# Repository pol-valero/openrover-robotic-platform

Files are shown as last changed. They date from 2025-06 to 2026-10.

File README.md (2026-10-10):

# OpenRover robotic platform

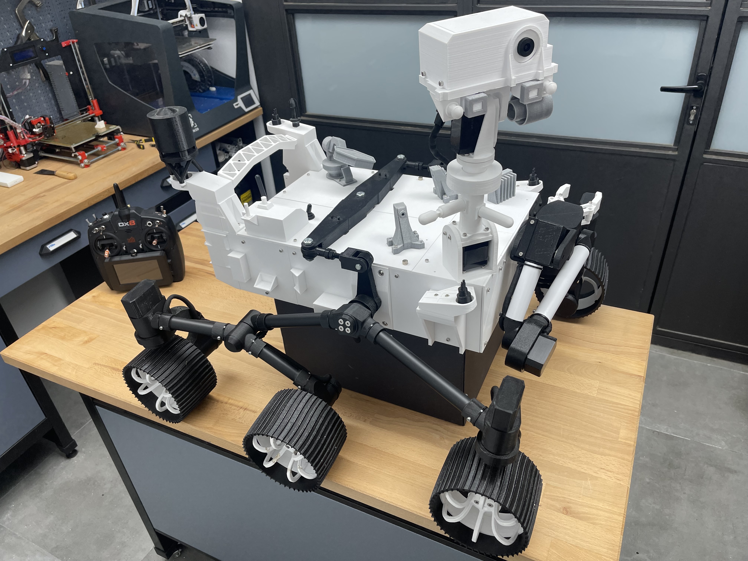
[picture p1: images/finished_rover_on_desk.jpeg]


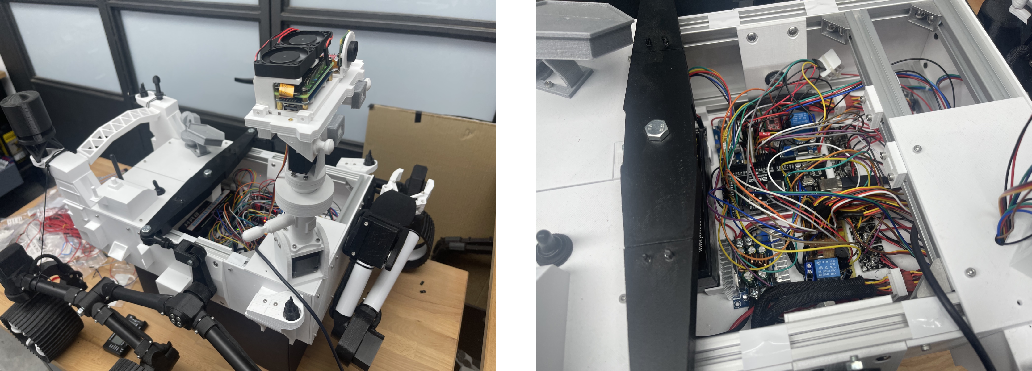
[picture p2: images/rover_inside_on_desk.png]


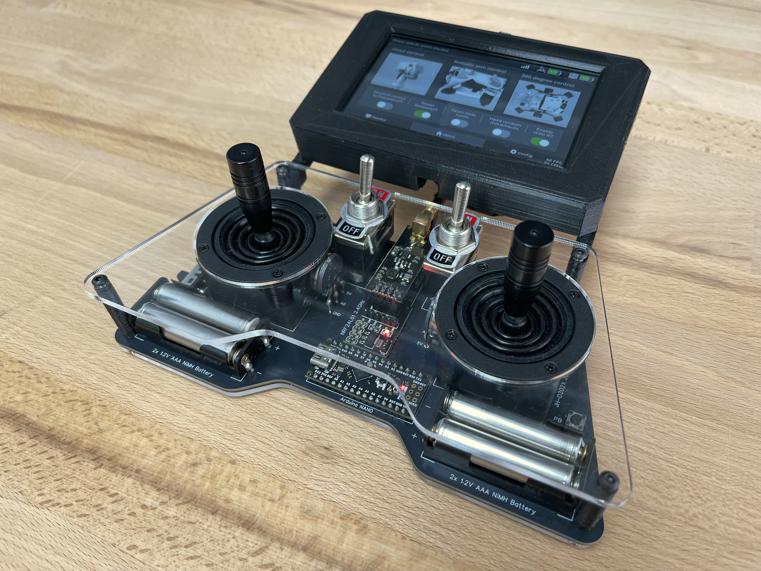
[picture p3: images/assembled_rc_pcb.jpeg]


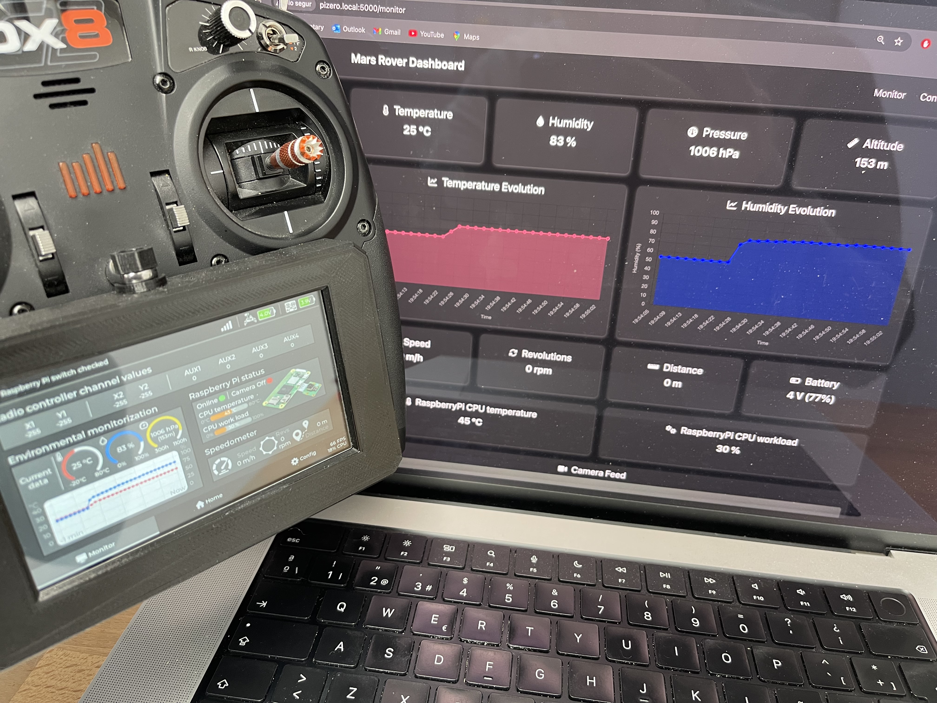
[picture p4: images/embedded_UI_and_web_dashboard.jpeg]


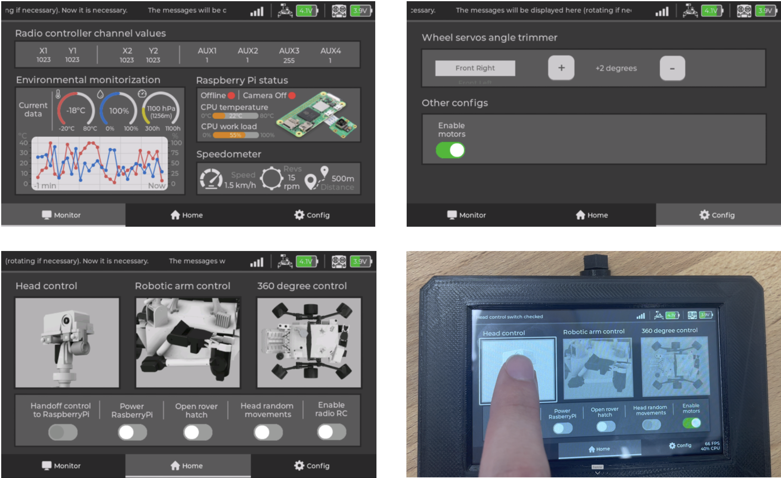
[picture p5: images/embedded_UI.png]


## Project overview

### Context
Rovers are planetary exploration robots that space agencies like NASA send to Mars or the Moon to explore and collect information, images, and samples. In this project, a functional 3D printed replica of the Mars "Perseverance" rover, which was launched by NASA in July 2020, is created. 

The OpenRover project was developed as part of my final computer engineering degree project. Therefore, in addition to the documentation provided in the repository’s READMEs, you can find a comprehensive [project report](project_report/openrover_project_report.pdf) containing theoretical explanations, design decisions, and technical implementation details (but the repository's READMEs provide enough information to replicate the project). 

### Objective
The main objective of the OpenRover project is to provide an extensible open-source robotic platform that allows anyone building it to put their DIY software/hardware/mechanical skills into practise, and to use popular development boards like Arduino, ESP32, and Raspberry Pi.  

As rovers are extremely sophisticated machines, they provide the perfect excuse to incorporate into the robotic platform several complex functionalities that replicate, at a smaller scale, the functionalities that real Mars rovers have (e.g., robotic arm, environmental sensors, 6-wheel drive, camera feed).  

### Key contributions
Although many similar open-source robotic projects already exist, even some also related to Mars rover robots, they tend to use a single type of development board. In the OpenRover project, several development boards are used among its main functional modules (e.g., RaspberryPi for web connectivity, ESP32 for embedded screen, Arduino for motor control) and there are interactions between these modules. 

This adds more educational value to the project, allowing to see some of the optimal usecases for each development board, and differentiates OpenRover from other open-source DIY robotic projects. 

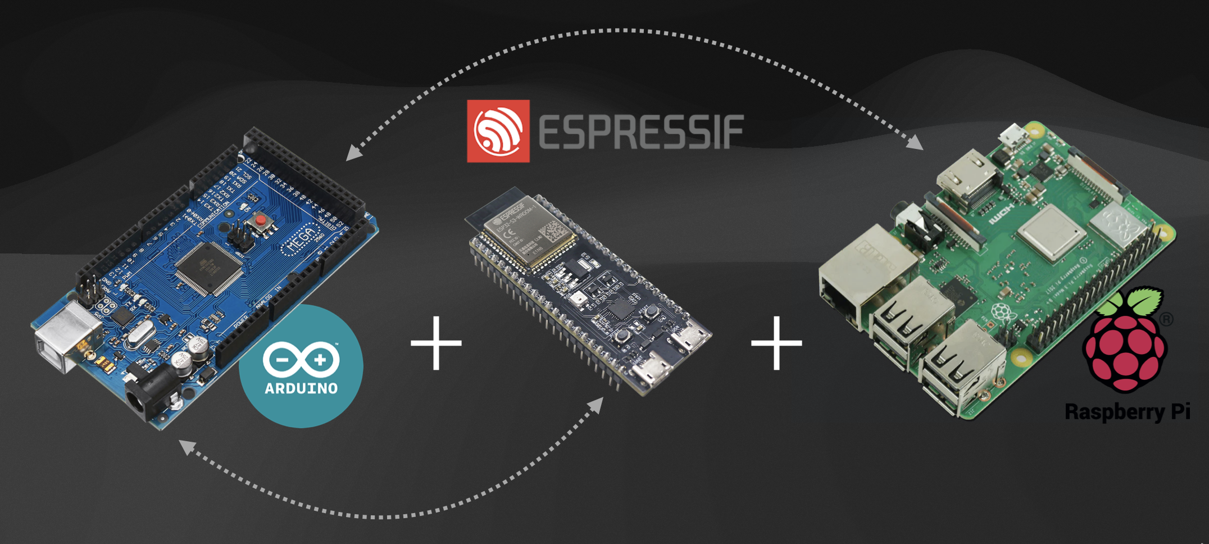
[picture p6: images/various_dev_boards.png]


### Tech stack

#### Programming languages and frameworks

 








#### Other technologies

To program Arduino and ESP32 microcontrollers, the PlatformIO IDE with the Arduino Framework was used. To create the embedded UI design of the touchscreen, the SquareLine Studio platform and LVGL library were used.

### Disclaimers
The rover's 3D design was originally made by a mechatronics engineer called Dejan, who owns an educational YouTube channel and website called "HowToMechatronics". This design was adapted and improved. 

**[Link to the original project used for the rover's 3D design](https://howtomechatronics.com/projects/diy-mars-perseverance-rover-replica-with-arduino/)**

The robotic arm's 3D design was extracted from a GitHub project made by Jakob Krantz, who also created a Mars rover replica. This design was adapted and improved. 

**[Link to the original project used for the robotic arm's 3D design](https://github.com/jakkra/Mars-Rover)**

All the OpenRover hardware and software was created from scratch, following a different approach from the one the creators of the original 3D designs followed. 

## Features

The OpenRover platform offers an interesting set of functionalities:

- 6-wheel drive platform with 4 steerable wheels
- 4-axis foldable robotic arm with gripper
- Tiltable and rotary head, with space for a development board and a camera
- Environmental sensors to measure temperature, humidity, pressure and altitude
- Custom remote control module with touchscreen, with a UI where status values are displayed and different operation modes can be selected
- Battery sensors for the rover and the custom remote control
- 4 main operation modes: conventional driving control, 360º turn control, robotic arm control, head control
- Web dashboard that displays status values and a video feed. This web dashboard is hosted in the rover

## Project modules
The OpenRover's components are organized, both at a hardware and software level, in different modules:

- [Central rover module](central_rover_module/): It has an Arduino Mega development board located inside the main body of the rover which manages all moving elements (e.g., motors, servomotors) as well as the rover's sensors and sending/receiving the radio signal.

- [Remote control and touchscreen module](remote_control_and_touchscreen_module/): It has an ESP32S3 development board that is responsible for managing the touchscreen, and an Arduino Nano that is responsible for reading the RC channel values, sending/receiving the radio signal and measuring battery levels. Two different remote control versions are available: a custom remote control PCB, or an attachment for a generic/commercial remote control.

- [Camera and webserver module](camera_and_webserver_module/): It has a RaspberryPi Zero 2W development board located inside the head of the rover. This board connects to a camera, generates a WiFi network and hosts a web dashboard.

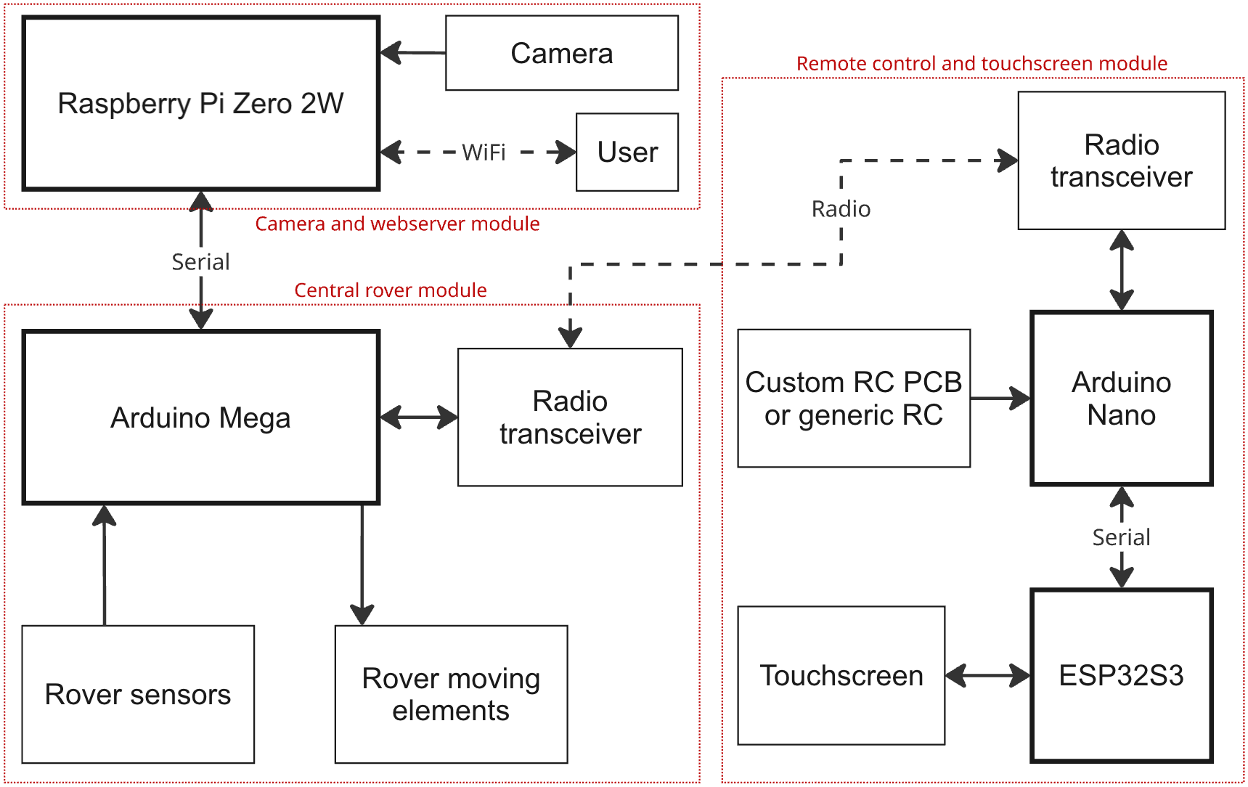
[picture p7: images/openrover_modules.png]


### Remarks
This repository contains the code and documentation of all the modules. However, the codebase is actually distributed across different repositories:

- The folder ``camera_and_webserver_module/raspberrypi_code/`` contains the [openrover-web-dashboard](https://github.com/pol-valero/openrover-web-dashboard.git) repository. 

- The folder ``central_rover_module/arduino_mega_code/`` contains the [openrover-central-controller](https://github.com/pol-valero/openrover-central-controller) repository. 

- The folder ``remote_control_and_touchscreen_module/pcb_remote_control/arduino_nano_code/`` contains the [openrover-rc-transmitter-pcb](https://github.com/pol-valero/openrover-rc-transmitter-pcb) repository. 

- The folder ``remote_control_and_touchscreen_module/generic_remote_control_attachment/arduino_nano_code/`` contains the [openrover-rc-transmitter](https://github.com/pol-valero/openrover-rc-transmitter) repository. 

- The folder ``remote_control_and_touchscreen_module/esp32s3_code/`` contains the [openrover-rc-touchscreen](https://github.com/pol-valero/openrover-rc-touchscreen.git) repository. 

- The folder ``remote_control_and_touchscreen_module/touchscreen_ui_design_squareline/`` contains the [openrover-touchscreen-ui-design](https://github.com/pol-valero/openrover-touchscreen-ui-design.git) repository. 

"Git subtrees" were used to link these independent repositories to folders inside this central [openrover-robotic-platform](https://github.com/pol-valero/openrover-robotic-platform) repository. 

## Expected build time
The build time can vary a lot depending on skill level and number of tools available. Experienced builders can expect to assemble the mechanical platform in approximately 60 hours and implement all the wiring and hardware in approximately 80 hours. 

Although the exact number of 3D printing hours was not recorded, it is estimated that it took approximately 400 hours to 3D print all the rover’s components. This number can vary a lot depending on the 3D printer model and the desired 3D printing quality.

## Getting started steps
- Step 1: Order all the mechanical and hardware parts. Lists with the most important parts are provided in the [hardware components](hardware_components/) folder.

- Step 2: 3D print the rover and remote controller parts present in the 3D design files, which are detailed inside the [3D designs](3d_designs/) folder.

- Step 3: Assemble the mechanical platform by joining the different 3D printed parts with the other mechanical parts (e.g., aluminium profiles, PVC tubes). A detailed guide for the mechanical assembly process of the rover is available in the [original project used for the mechanical design](https://howtomechatronics.com/projects/diy-mars-perseverance-rover-replica-with-arduino/). Images showing the assembly of the modified OpenRover design and custom remote control are available in the [assembly folder](assembly/).

- Step 4: Create the wiring connections for the hardware components (e.g., motors, servomotors) and between the hardware electronics (e.g., Arduino Mega, motor drivers). In each of the OpenRover's modules folders ([central rover](central_rover_module/), [remote control and touchscreen](remote_control_and_touchscreen_module/), and [camera and webserver](camera_and_webserver_module/)), schematics of the wiring connections are found. Images showing the soldering of various boards, the creation of electrical connections, and the placement of hardware components can be found in the README of the [assembly folder](assembly/).

- Step 5: Set up and upload the code to the development boards. In each of the OpenRover's modules folders ([central rover](central_rover_module/), [remote control and touchscreen](remote_control_and_touchscreen_module/), and [camera and webserver](camera_and_webserver_module/)), additional README files detail the necessary steps for getting all the OpenRover's software up and running for the module.

## Demos
| |  |
| --- | --- |
|  |  |
|  |  |

### Longer demo video
Here is a longer demo video where some of the possible movements can be seen: https://www.youtube.com/watch?v=uD4_qy3aUkQ

Preview of demo video at 2x speed: 



### More images
On the [sciencefairs and makerfaires images](images/sciencefairs_and_makerfaires_images/) folder, there are some more images of the rover in action as well as an image detailing how the rover can be disassembled for easier transport. 

## Take it to the next level
Now it is your time to build upon the OpenRover platform. One of the cores ideas behind OpenRover is that people who replicate the project are able to modify and improve the platform, as it is designed to be very modular and extensible, specially on the software related side. 

You can add your own upgrades to the robot, integrating new components and developing additional features. 

Here are some ideas to spark inspiration for expanding OpenRover's functionalities:

- Rover control from the web dashboard (e.g., using draggable joysticks), which currently is only used for monitoring and displaying video feed

- Adding computer vision using the existing RaspberryPi camera and RaspberryPi Zero 2W board. Computer vision could be used to navigate autonomously or to track objects with the rover's tiltable and rotary head

- Ability to record movements for the robotic arm, allowing it to automatically fold and unfold or perform a certain procedure

- From the hardware schematic designs of the rover, design PCB boards that can be manufactured. These boards would be very useful to make the hardware connections more compact and to allow an easier replication of the project

<br/>

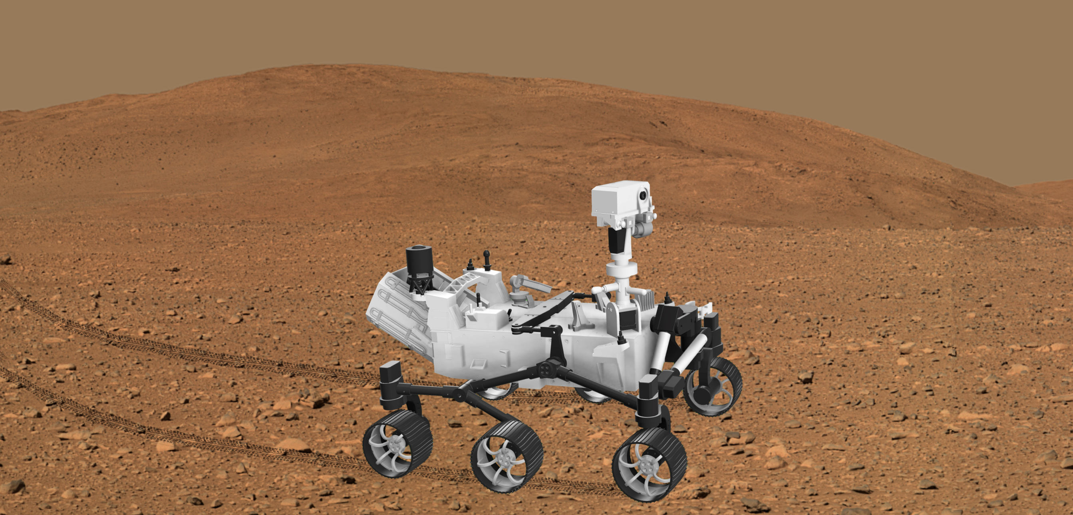
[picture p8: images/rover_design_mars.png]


## Licensing
Licensed under [MIT License](LICENSE.txt)

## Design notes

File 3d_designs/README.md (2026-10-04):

## 3D designs remarks

The original 3D design of the Mars rover model can be found in this [Cults3D page](https://cults3d.com/en/3d-model/game/mars-rover-perseverance-replica-howtomechatronics). The original 3D design of the robotic arm can be found in this [GitHub page](https://github.com/jakkra/Mars-Rover). Lots of modifications were made to these designs, which were originally created by Dejan (HowToMechatronics) and Jakob Krantz respectively.

Since the original design of the Mars rover is not free (it has to be purchased via the Cults3D page provided before) only the parts of the rover that were created from scratch are present in the [rover Fusion360 design file](rover_modified_and_new_parts.f3d) of this folder. Since the original design of the robotic arm is open-source, the [rover Fusion360 design file](rover_modified_and_new_parts.f3d) contains the parts of the robotic arm that were either created from scratch, modified or original. 

For the remote control and touchscreen module, there are two different 3D designs depending on the selected option:

1) Custom remote control PCB: This [Fusion360 design file](rc-pcb-spacers-and-touchscreen-case.f3d) contains the spacers that hold the acrylic plates and PCB together, the structure that holds the touchscreen, and the case for the ESP32S3-8048 touchscreen.

2) Generic/commercial remote control attachment: The cases for the home-made PCB (of the "Arduino Nano" submodule) and for the ESP32S3-8048 touchscreen are in this [Fusion360 design file](rc_and_touchscreen_cases-spektrum_dx8.f3d). These cases adapt to the shape of the Spektrum DX8 remote, allowing to place the home-made PCB and touchscreen as an attachment. 

The case for the ESP32S3-8048 touchscreen is a modified version of this [case design](https://www.thingiverse.com/thing:6517481) found on Thingiverse.

## 3D designs images

### DIY Perseverance Rover Replica design with some new and modified parts
  <p align="center">
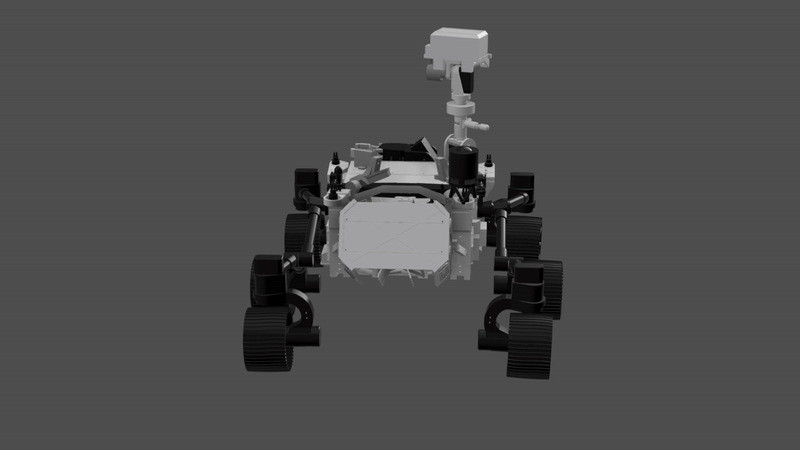
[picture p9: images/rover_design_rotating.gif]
animated
    
  </p>

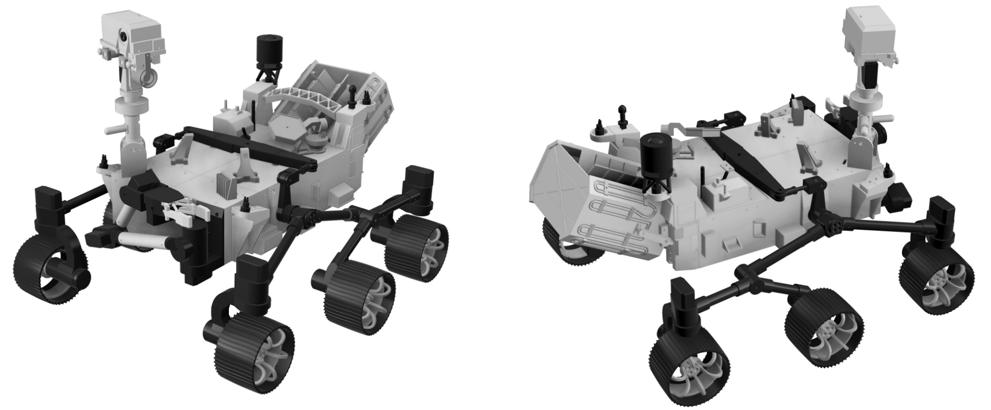
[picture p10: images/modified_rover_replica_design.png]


### Original (left) and modified (right) robotic arm design
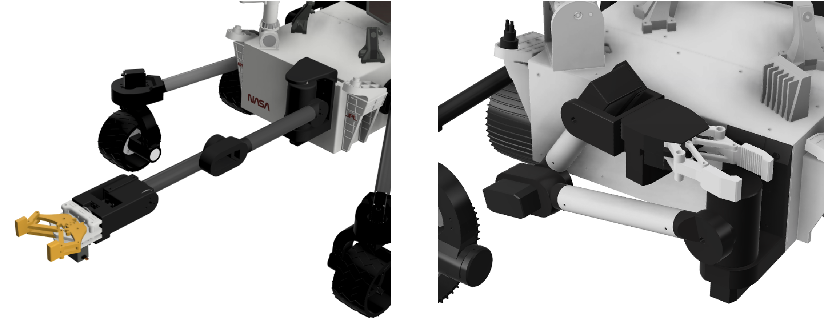
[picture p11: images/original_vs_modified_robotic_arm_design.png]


### Spacers, touchscreen case, and structure design for the custom remote control PCB 
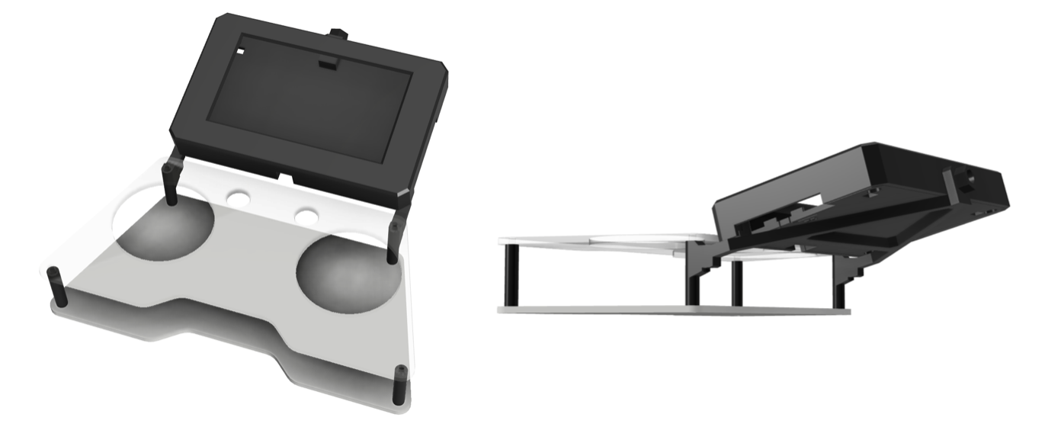
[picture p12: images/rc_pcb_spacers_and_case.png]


### Attachment cases design for the generic/commercial remote control 
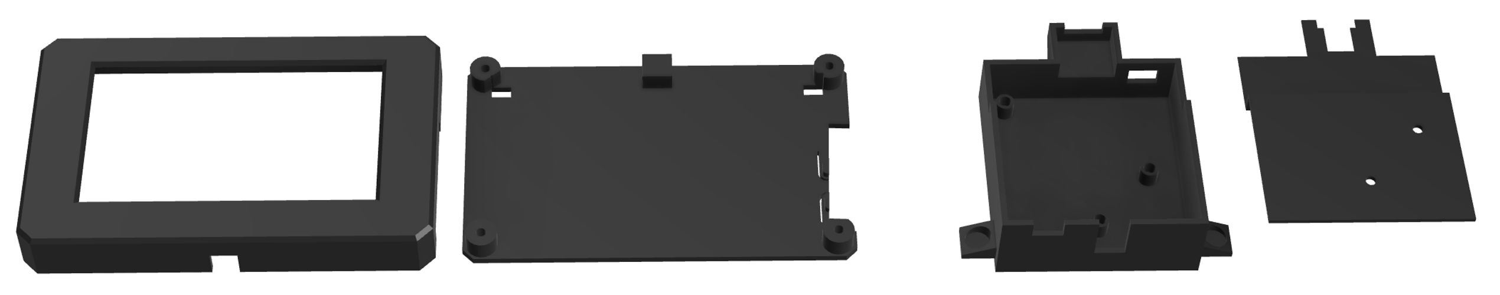
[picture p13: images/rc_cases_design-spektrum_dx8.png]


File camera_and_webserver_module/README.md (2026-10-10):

# Camera and webserver module
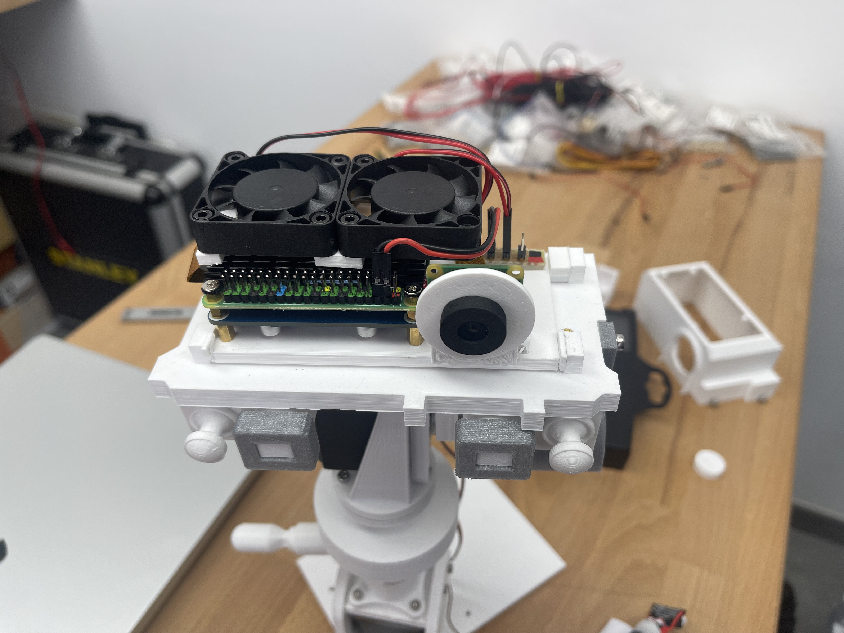
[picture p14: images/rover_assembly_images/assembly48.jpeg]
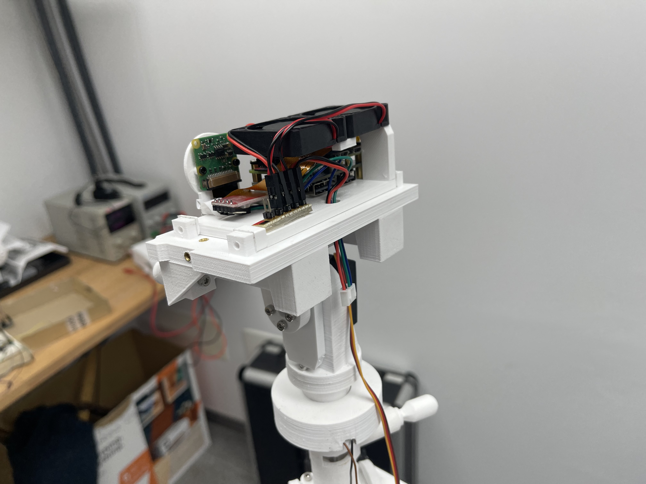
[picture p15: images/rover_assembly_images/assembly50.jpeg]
|  |  |
| --- | --- |

## Code setup guide
Before uploading this module's project code in the RaspberryPi Zero 2W, it is necessary to install and OS in the board. Specifically, the RaspberryPi OS Lite (headless version) has to be installed. This OS and an install guide can be found in the [RaspberryPi website](https://www.raspberrypi.com/software/operating-systems/).

Once the Raspberry Pi OS is running and SSH connections can be made to be the board, it is possible to upload all the module's project code. To upload an edit the code, the best way is to install the SFTP plugin for the Visual Studio Code editor. This plugin allows to easily set up and modify the project’s file structure and file’s contents remotely from a standard PC. 

Once the whole project is uploaded, you have to go inside the main project folder and execute the following command. 

```python -m logic.main```

If it is the first time you execute this command, several errors will displayed, detailing the dependencies used by the code that need to be installed. It is recommended to install this dependencies on a "virtual environment". Once these dependencies are installed, if we execute the previous command, this module's program will start running, stablishing serial communication with the Arduino Mega and generating the web dashboard. 

The web dashboard will be available on the following URL. 
```http://pizero.local:5000/monitor```

If instead of the RaspberryPi connecting to an existing WiFi, you want the RaspberryPi to generate a WiFi network on its own, the following command needs to be used.   
```sudo nmcli device wifi hotspot ssid RoverWiFi password marsRover```

Optionally, the commands to generate the WiFi network and to execute the module's program can be written into a script. This script can then be called inside the ```/etc/rc.local``` file, which is executed at startup. This way, once the RaspberryPi Zero 2W is powered, it will generate the WiFi network and execute the module's program automatically. You can find and example startup script in the [raspberrypi_code/scripts/](raspberrypi_code/scripts/) folder.

It is important to make sure that the wiring connections to the RaspberryPi Zero 2W are exactly the same as the ones detailed in the wiring schematic of this module.

## Web dashboard UI design
The implemented monitoring screen can be seen in the image below. 

![Alt text](/images/web_dashboard_computer.png)

The web dashboard design is responsive and adapts to different screen sizes, as seen in the images below. 

![Alt text](/images/web_dashboard_mobile.png)

## Hardware and schematics
The hardware present on the camera and webserver module includes a RaspberryPi Zero 2W board that is responsible for receiving camera input, creating a WiFi network with a self-hosted website available in it and sending/receiving communications via serial (to/from Arduino Mega).

In this [schematic](camera_and_webserver_module_schematic.pdf), all the hardware present on this module can be seen.

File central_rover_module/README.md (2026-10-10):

# Central rover module
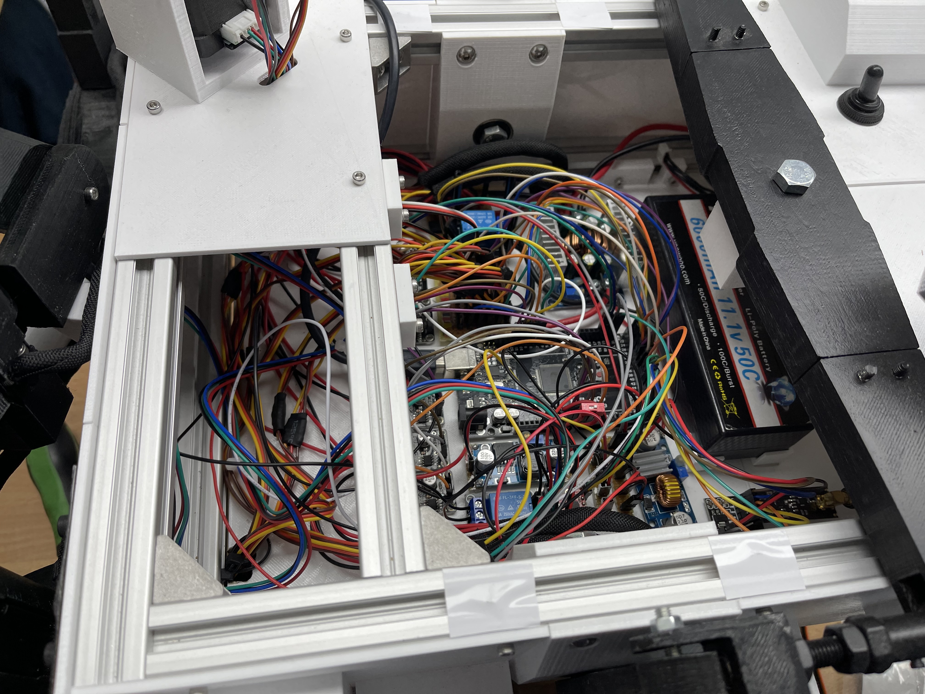
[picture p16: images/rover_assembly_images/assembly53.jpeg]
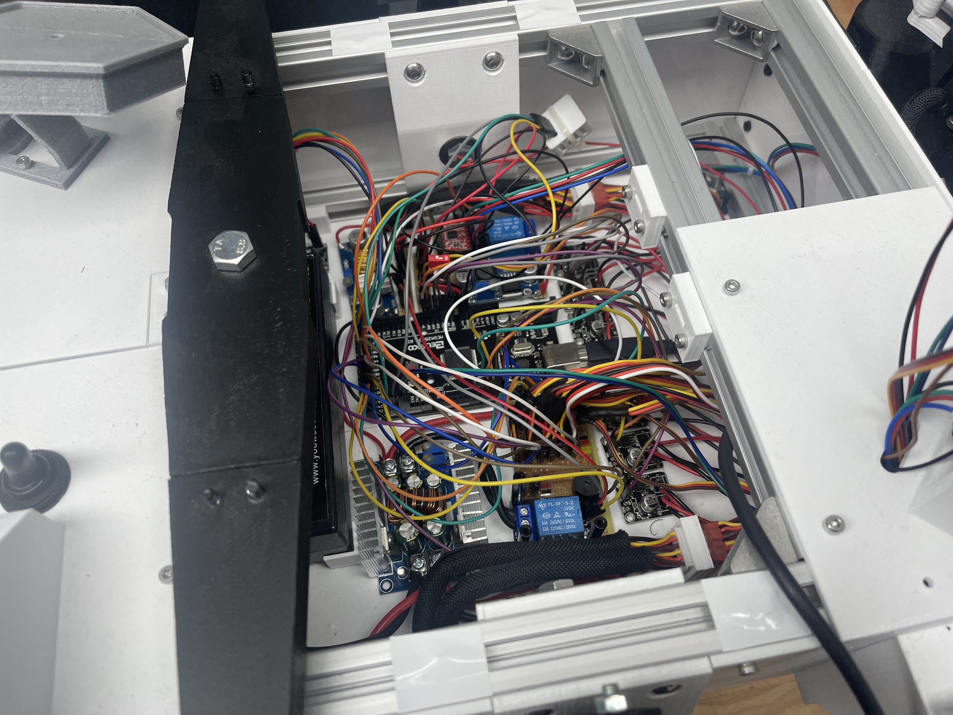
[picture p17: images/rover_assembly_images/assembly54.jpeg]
|  |  |
| --- | --- |

## Code setup guide
To develop the code for this module, the PlatformIO IDE was used. This IDE is integrated into the versatile Visual Studio Code editor, and can be installed simply by searching "PlatformIO IDE" in the "Extensions" tab of Visual Studio Code. 

Thanks to the use of PlatformIO, all the code, configuration files, and dependencies are in a single package. This makes it very easy to share the complete project, enabling other people to execute it right after they download it. 

Therefore, just by opening the project present in this folder with PlatformIO, connecting the Arduino Mega development board via USB, and clicking the "upload" button, the code will be uploaded to the Arduino Mega and will start executing. 

The only thing that needs to be taking into account is making sure that the wiring connections to the Arduino Mega are exactly the same as the ones detailed in the  wiring schematic of this module. 

## Hardware and schematics
The hardware present on the central rover module includes an Arduino Mega development board that is responsible for managing all the moving elements (e.g., servomotors, motors, stepper motor), reading the environmental sensor’s values and sending/receiving communications via serial (to/from RaspberryPi Zero board) and via radio (to/from custom RC). 

In this [schematic](central_rover_module_schematic.pdf), all the hardware present on this module can be seen.

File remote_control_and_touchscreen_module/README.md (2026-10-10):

# Remote control and touchscreen module

## Remote control options
The OpenRover project has two remote control options available:

1) Custom remote control created from scratch, using a manufactured double-layer PCB, some 3D printed parts, and acrylic plastic. Code, schematics, and further info can be found in this [folder](pcb_remote_control/). 

2) Custom attachment for a generic/commercial remote control that has a PPM output port, like the Spektrum DX8, using a home-made PCB and some 3D printed parts. Code, schematics, and further info can be found in this [folder](generic_remote_control_attachment/).

For anyone trying to replicate the project, I would definitely recommend choosing the first option. The second option would only be suited for those who already have a Spektrum DX8 (or similar) remote control, really like how it feels/handles, and would like to tinker with it. For the second option, also note that from my experience, the PPM readings can be a little unreliable sometimes.

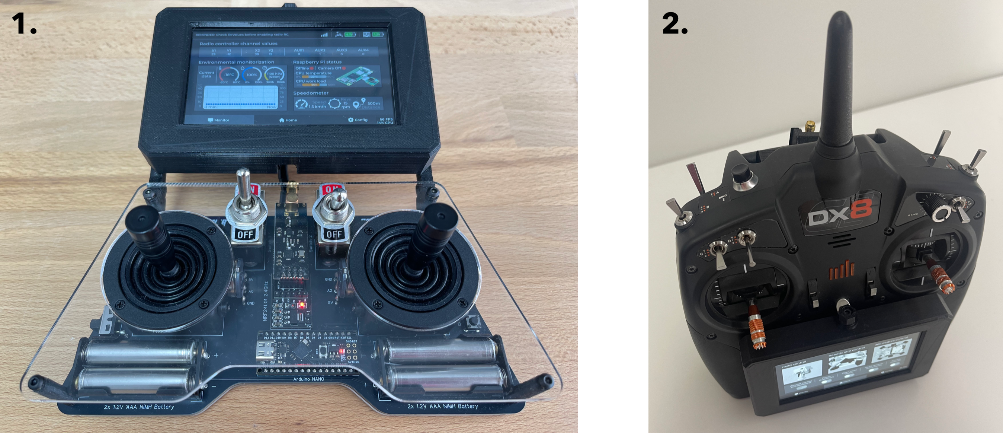
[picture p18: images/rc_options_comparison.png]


## Code setup guide
No matter which remote control option is selected, this module is formed by two submodules, the "Arduino Nano" and the "ESP32S3 touchscreen" submodules. The [code](esp32s3_code/) and [embedded UI design](touchscreen_ui_design_squareline/) of the "ESP32S3 touchscreen" submodule is exactly the same for the two remote control options, that's why they are located in this folder. The code and schematics of the "Arduino Nano" submodule and the schematics of the "ESP32S3 touchscreen" submodule differ depending on the chosen remote control option, that's why they are located inside the folder of each remote control option.

To develop the code for these submodules, the PlatformIO IDE was used. This IDE is integrated into the versatile Visual Studio Code editor, and can be installed simply by searching "PlatformIO IDE" in the "Extensions" tab of Visual Studio Code. 

Thanks to the use of PlatformIO, all the code, configuration files, and dependencies are in a single package. This makes it very easy to share the complete project, enabling other people to execute it right after they download it. 

Each of the two submodules is a standalone PlatformIO project. Therefore, just by opening the project present in this folder (and in the chosen RC option subfolder) with PlatformIO, connecting the ESP32S3 or Arduino Nano development board via USB, and clicking the "upload" button, the code will be uploaded to the ESP32S3 or Arduino Nano and will start executing. 

The only thing that needs to be taking into account is making sure that the wiring connections of the ESP32S3 and the Arduino Nano are exactly the same as the ones detailed in the wiring schematics of this module, which can be found inside the folder of each remote control option. 

## Embedded UI design
To create the embedded UI design of the touchscreen, the SquareLine Studio platform and LVGL library were used. To edit the UI, these steps have to be followed:

- Step 1: Open the [SquareLine Studio project](touchscreen_ui_design_squareline/) and make the desired visual changes

- Step 2: Click on Export -> Export UI Files. The UI files export path must be previously specified in the "Project Settings"

- Step 3: Copy all the exported UI Files into the "squareLineFiles" folder of the [ESP32S3 PlatformIO project](esp32s3_code/), making sure to overwrite the previous files that were in this folder

- Step 4: Click the "upload" button in PlatformIO to upload the code to the ESP32S3. The modified UI should now appear on the touchscreen. 

Three screens have been implemented in the embedded UI: Control, Monitor and Configuration. These screens can be seen in the images below. 

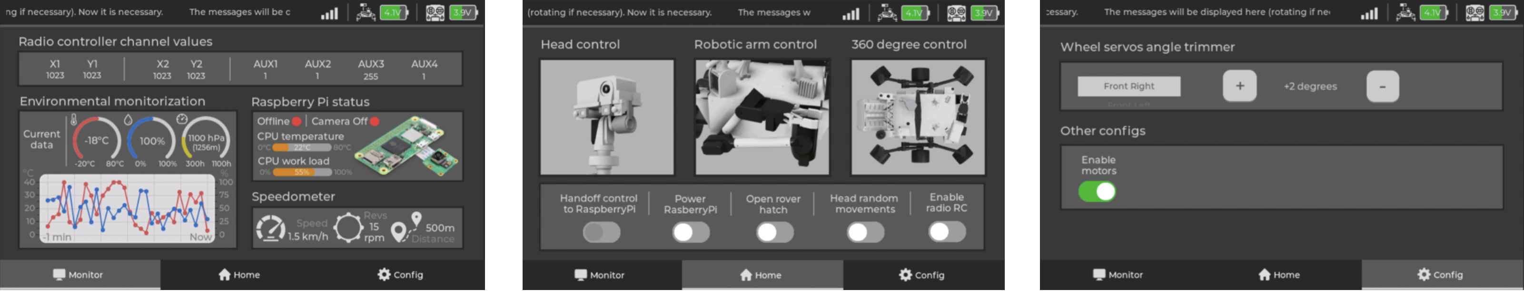
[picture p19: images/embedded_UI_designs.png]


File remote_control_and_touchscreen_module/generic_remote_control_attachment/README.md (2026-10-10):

# Attachment for a generic/commercial remote control
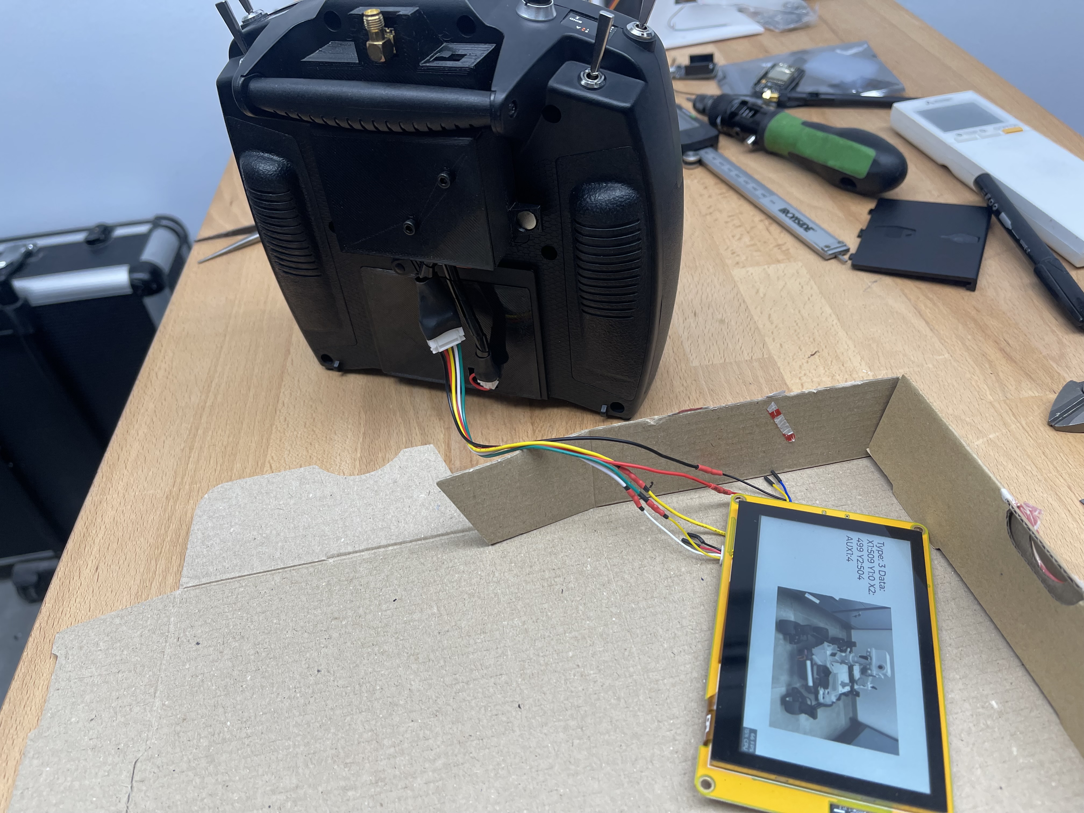
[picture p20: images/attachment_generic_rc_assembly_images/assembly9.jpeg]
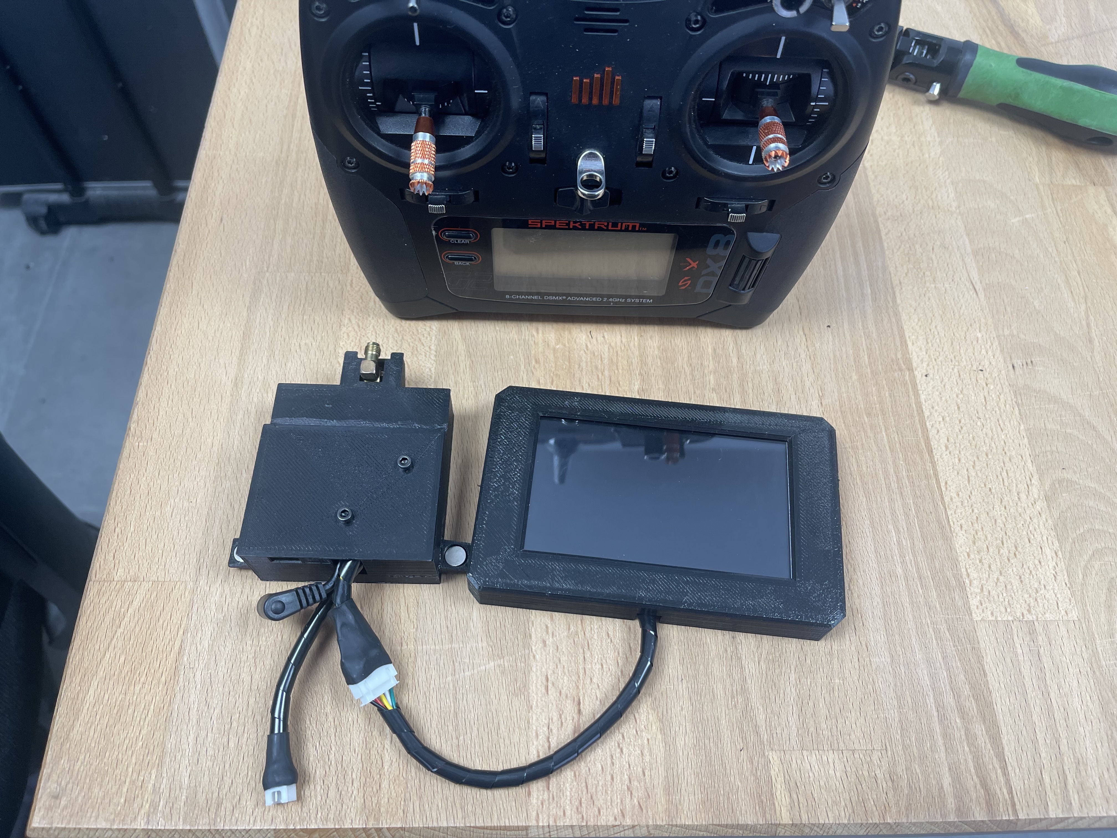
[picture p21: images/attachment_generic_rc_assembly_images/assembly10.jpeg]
|  |  |
| --- | --- |

## Remarks
For this remote control option, the developed remote control and touchscreen module is an attachment for any generic/commercial RC that has a PPM output port (usually known as "Trainer Port"). The RC model that I have personally used is the Spektrum DX8 (if another model wants to be used, the 3D printed parts would have to be adapted). 

This trainer port usually is a 3.5mm audio jack, but it is not a standard port and could also be a mini-USB, depending on the brand. The transmitters usually use PPM (Pulse Position Modulation) signals outputted from this “Trainer port” to transmit each of the RC channel values.

With the help of an Arduino Nano, these PPM signals can be processed by the custom attachment that was developed. This way, the radio module of the generic RC is not used, and the only purpose of the generic RC is to send the values of its different channels (e.g., joysticks, switches…) via PPM, so that the custom attachment can receive them. In turn, this custom attachment uses an NRF24 radio transceiver to send the channel values to the rover using a custom communication protocol. 

## Hardware and schematics
For this option (generic remote control attachment), the hardware present in this module includes an ESP32S3 development board that is responsible for managing the screen and an Arduino Nano board that processes the RC PPM signals, reads the battery voltage, and controls the radio transceiver. 

The touchscreen model is the ESP32S3_8048S043, with a resolution of 800 x 480 px and 4.3" screen size. This model has an ESP32S3 and I/O connectors built in.

This is the [schematic](rc_and_touchscreen_module_schematic-generic_remote.pdf) for this remote control option, where all the hardware present on this module can be seen.

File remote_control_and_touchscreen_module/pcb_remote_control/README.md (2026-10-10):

# Custom remote control PCB
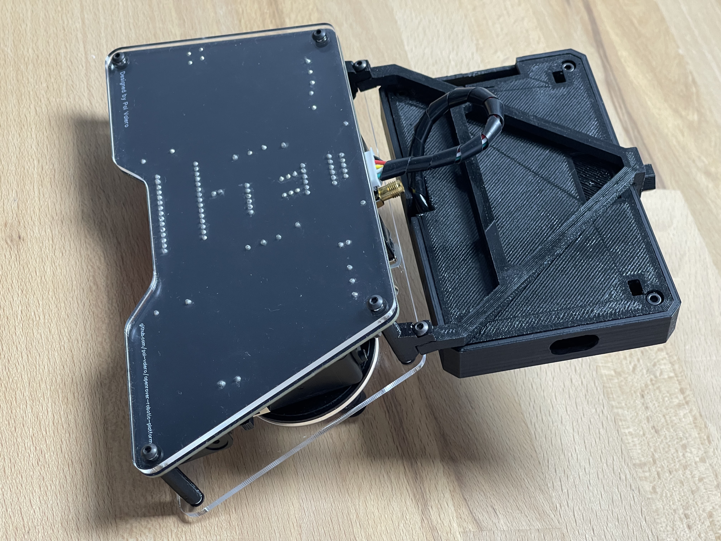
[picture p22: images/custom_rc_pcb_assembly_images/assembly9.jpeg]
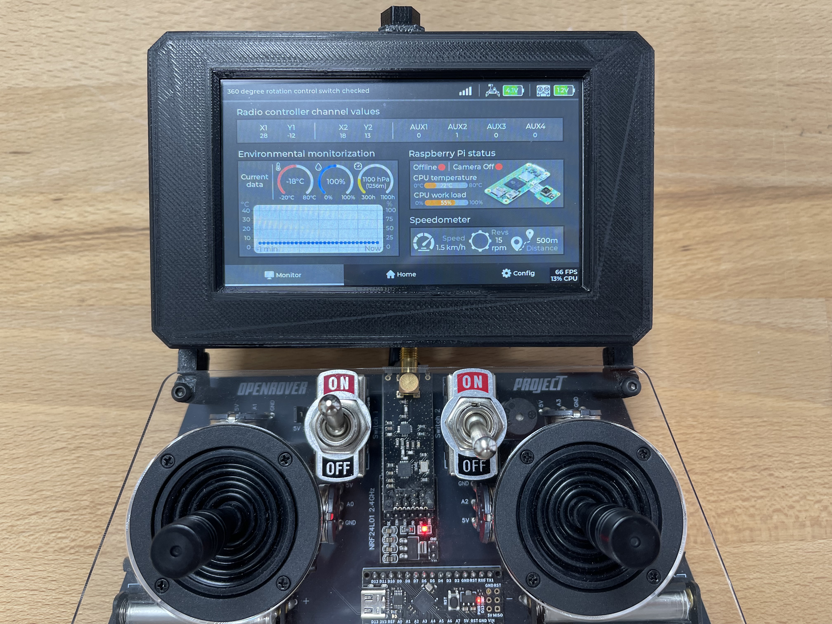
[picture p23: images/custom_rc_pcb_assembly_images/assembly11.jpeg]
|  |  |
| --- | --- |

## Remarks
For this remote control option, the developed remote control and touchscreen module is built using a custom double-layer PCB. The [PCB design](remote_control_pcb_design_easyeda.json) has been created using the EasyEDA app, and the PCB has been manufactured by JLCPCB. 

In order to manufacture the PCB, a [Gerber fabrication file](remote_control_pcb_gerber.zip) has to be generated from the design and then has to be uploaded to the manufacturer's website (e.g., JLCPCB, PCBWAY...). If you want to make any modifications to the EasyEDA PCB design, you will have to regenerate the Gerber by going into the top menu and selecting "Fabrication -> PCB Fabrication File (Gerber) -> Generate Gerber".

Other parts of the remote control that have to be manufactured are the top and bottom acrylic plates, which should be cut using a laser or CNC machine. In my case, I used a workshop near my home that had a laser machine, but there are also online websites where you can order laser cut designs in acrylic. These are the designs for the [top](rc_top_plate.dxf) and [bottom](rc_bottom_plate.dxf) acrylic plates. I would recommend using 3mm clear acrylic.     

## Hardware and schematics
For this option (custom remote control PCB), the hardware present in this module includes an ESP32S3 development board that is responsible for managing the screen and an Arduino Nano board that reads the analog or digital signals from the joysticks/switches/buttons, reads the battery voltage, and controls the radio transceiver. 

The touchscreen model is the ESP32S3_8048S043, with a resolution of 800 x 480 px and 4.3" screen size. This model has an ESP32S3 and I/O connectors built in.

This is the [schematic](esp32s3_touchscreen_submodule_schematic-pcb_remote.pdf) of the "ESP32S3 touchscreen" submodule for this remote control option. The [EasyEDA PCB design](remote_control_pcb_design_easyeda.json) can be seen as the schematic of the "Arduino Nano" submodule. 

Here are a couple images of the top and bottom layers of the EasyEDA PCB design:
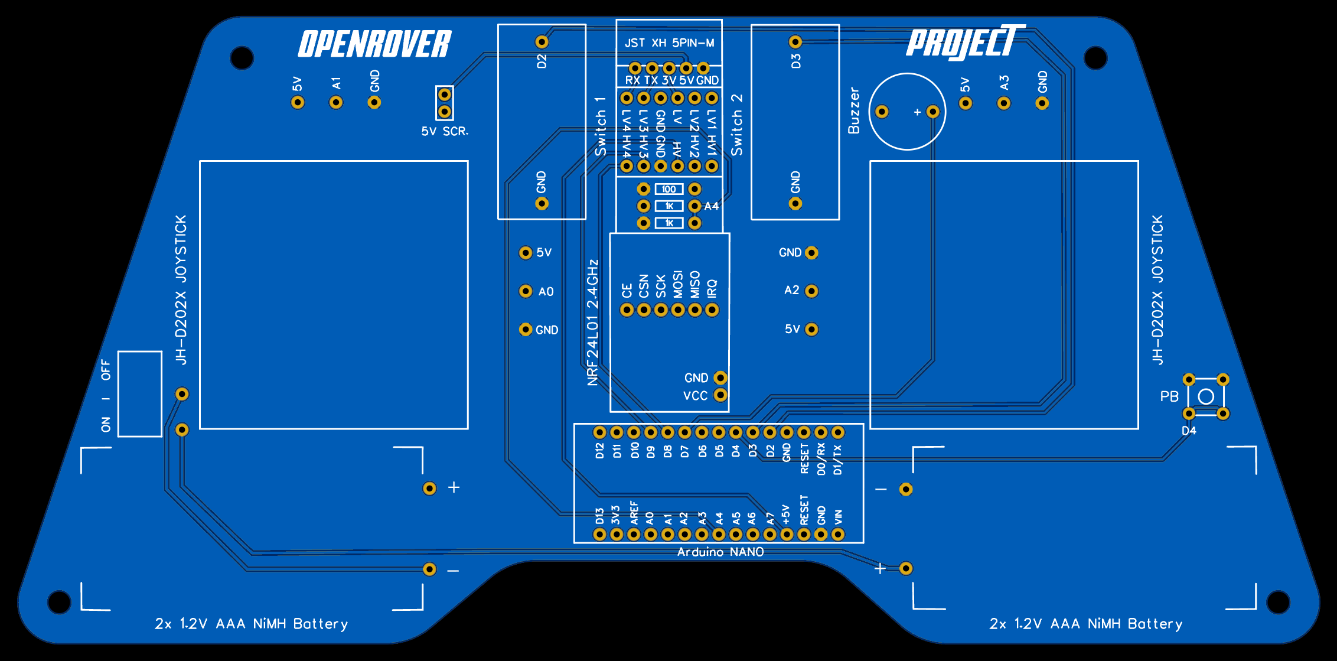
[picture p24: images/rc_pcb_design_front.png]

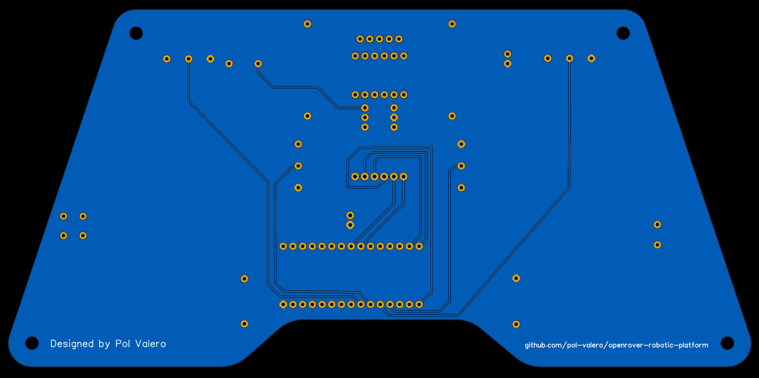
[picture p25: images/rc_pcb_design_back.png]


## Short demo


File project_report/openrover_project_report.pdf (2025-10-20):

# OpenRover: A 3D-printed open-source robotic platform for software and hardware development

# Pol Valero Arjona

# La Salle Campus Barcelona – Grau en Enginyeria Informàtica

# Barcelona, Juny 2025

i

# Abstract

Rovers are planetary surface exploration robots that space agencies like NASA send to Mars in order to explore and collect information that will be sent back to Earth.

This final degree project originates from a personal hobby project in which, using an existing 3D design of a Mars rover replica found online, the design has been adapted, improved, 3D printed and assembled at home. The final 3D printed result has the functional structure and appearance of the "Perseverance" rover, which was launched by NASA in July 2020, and landed on Mars in February 2021.

The main objective of the final degree project is to develop an open-source robotic platform that can enable anyone who tries building it to learn more about both the software and hardware aspects of DIY robotic projects, specially using and learning about widely adopted microcontrollers such as "Arduino" and "ESP32". As rovers are extremely sophisticated machines, they provide the perfect excuse to incorporate into the robotic platform several complex functionalities that replicate, at a smaller scale, the functionalities that real Mars rovers have (e.g., robotic arm, environmental sensors, 6-wheel drive).

Although many open-source robotic projects already exist (even some also related to Mars rover robots), they usually only use a single type of development board. In the developed OpenRover project, partly due to its complexity and wide scope, several development boards are used among its main functional modules (e.g., RaspberryPi for web connectivity, ESP32 for embedded screen, Arduino for motor control) and there are interactions between these modules. This adds more educational value to the project, allowing to see each development board optimal usecase, and differentiates OpenRover from other open-source DIY robotic projects.

Starting from the 3D printed structure of the rover, this project has incorporated into the rover all the hardware (e.g., motors, microcontrollers, sensors) as well as developed all the software (e.g., web dashboard for monitorization, creation of communication protocols between modules, generation of control signals for motors) that is necessary in order to operate the rover remotely. Additionally, a remote control module with a touchscreen has also been developed, which serves both as a means to operate the rover and to monitor its status in a graphical way.

The project has been named OpenRover, due to the "open source" nature of the project. OpenRover has been able to meet its main objective, as the created robotic platform and remote control module have incorporated several interesting functionalities using different development boards (Arduino, ESP32, RaspberryPi), making this project a useful resource for people wanting to learn more about the DIY robotics field, or for those who want to replicate and build upon the OpenRover robotic platform.

Keywords – Robotics, RaspberryPi, Arduino, ESP32, LVGL, Web dashboard, Embedded system

viii

ix

# Contents

x

xi

6.1 | Temporal costs | 88
6.2 | Economic costs | 89
7 | Conclusions | 90
8 | Future lines of work | 92
9 | References | 94
Annex I | 99
Annex II | 104

xii

# List of figures

Figure 6. Rover modified design and assembled mechanical structure (own elaboration of images

Figure 18. Key header and implementation files for central rover module (own elaboration) . 55

Figure 21. Central rover module “Execute frame type functions” activity (own elaboration)... 58

Figure 25. SquareLine studio components with default theme and configuration (own

Figure 27. Key header and implementation files for ESP32S3 and touchscreen submodule (own

Figure 28. Library headers and main.cpp file for Arduino Nano submodule (own elaboration) 66 Figure 29. ESP32S3 and touchscreen submodule main activity diagram (own elaboration) ..... 66 Figure 30. ESP32S3 and touchscreen submodule “Execute frame type functions” activity (own

Figure 31. ESP32S3 and touchscreen submodule buttons and switches flow (own elaboration)

Figure 34. Key implementation files and libraries for camera and webserver module (own

Figure 36. Camera and webserver module “Handle received frames thread” activity (own

xiii

Figure 37. Camera and webserver module “Manage status data thread” activity (own
elaboration) | 72
Figure 38. Camera and webserver module “Flask webserver threads” activity (own elaboration)
| 73
Figure 39. Web dashboard monitor screen (own elaboration) | 76
Figure 40. Web dashboard in mobile browser (own elaboration) | 77
Figure 41. Web dashboard and embedded UI comparison (own elaboration) | 77
Figure 42. RaspberryPi startup bash script (own elaboration) | 78
Figure 43. Tasks timing using non-blocking “millis()” template (own elaboration) | 81
Figure 44. C++ (left) and Python (right) frame structure (own elaboration) | 81
Figure 45. Frame types definition C++ header file (own elaboration) | 82
Figure 46. Project’s time distribution pie chart (own elaboration) | 88
Figure 47. Project’s Gantt diagram (own elaboration) | 89
Figure 48. Original DIY Perseverance Rover Replica design (own elaboration of images and
original design extracted from [9] ) | 99
Figure 49. Original (left) and modified (right) Jakob Krantz arm design (own elaboration of images
and original designs extracted from [9] [10] ) | 99
Figure 50. Modified DIY Perseverance Rover Replica design (own elaboration of images and
original design extracted from [9] ) | 100
Figure 51. Organized set of OpenRover’s 3D printed pieces (own elaboration) | 100
Figure 52. OpenRover body assembly (own elaboration) | 101
Figure 53. Custom remote control cases design (own elaboration) | 102
Figure 54. 3D-printed remote-control cases (own elaboration) | 102
Figure 55. Original (left) and modified (right) interior head design (own elaboration of images
and original design extracted from [9] ) | 103
Figure 56. Interior head components placement (own elaboration) | 103

xiv

# List of tables

Table 1. Arduino boards comparison (own elaboration with data extracted from [19] ) | 18
Table 2. ESP32 SoC comparison (own elaboration with data extracted from [20] ) | 19
Table 3. Teensy boards comparison (own elaboration with data extracted from [23] ) | 20
Table 4. RaspberryPi boards comparison (own elaboration with data extracted from [26] ).... 20
Table 5. OpenRover components cost (own elaboration) | 105

xv

# Acronyms

ADC: Analog to Digital Converter

AP: (WiFi) Access Point

BOM: Bill Of Materials

CSI: Camera Serial Interface

DIY: Do It Yourself

FFC: Flat Flexible Cable

FPV: First Person View

FPS: Frames Per Second

GPIO: Global Purpose Input Output

GUI: Graphical User Interface

I/O: Input Output

IDE: Integrated Development Environment

LORA: Long Range module

OOP: Object Oriented Programming

OS: Operating System

PCB: Printed Circuit Board

PWM: Pulse Width Modulation

RC: Remote Control

RTOS: Real Time Operating System

SoC: System on Chip

STL: Standard Triangle Language

VCS: Version Control System

xvi

# 1 Introduction

# 1.1 Project motivation and origin

This final degree project originates from a personal project of mine that started nearly 2 years ago, in the summer of 2023. For a long time, I have had a passion for tinkering with electronics and coding, and in my free time I have developed all kinds of DIY projects. Besides experimenting with electronics and programming, I have also enjoyed designing and 3D printing components for these at-home DIY hobby projects.

As my Computer Engineering degree was coming to an end, I felt the need to create a project that combined all my existing knowledge in 3D design, 3D printing and mechanical assembly with the more electronics and software related knowledge that I had acquired during my degree. That is why I started looking for a project that could be complex enough to be a challenge and where I could spend a lot of time not only developing the hardware aspect of the project, but the software aspect as well.

After extensive research on the internet, looking for already existing open-source projects and taking interesting insights from each of them, I found a project idea that met my needs. This project was called "DIY Mars Perseverance Rover Replica", and it was created by a mechatronics enthusiast who spent a lot of time making a very detailed and 3D-printable functional model of a Mars rover. He also created a website and some videos showing how to assemble the 3D printed model and how to put some essential hardware components and a microcontroller to make the model operational.

One might think that since this enthusiast did the 3D design, mechanical assembly guides, put some hardware and created code for a microcontroller, there would be no point in taking this project as a starting point for another project, as most of the work would already be done. However, after careful consideration, I ended up thinking that this was not necessarily the case. First of all, the project creator had made a very detailed and functional mechanical platform, but the electronic hardware and coding aspects of the project were far from complex. The operational functionalities that he ended up implementing were very limited, only being able to operate the rover with an existing generic remote control, and not adding any sort of sensors nor complex functionalities. He did implement a camera for the rover, but it was also very basic and only broadcasted low quality analog video using a FPV drone transmitting module. Secondly, the mechanical and 3D printed design left lots of room for expansion; for example, he had not implemented any sort of robotic arm (which real Mars rovers have) nor cable management system.

This is why I finally decided to take this existing project as a starting point for my personal project. It is important to mention that I only replicated the mechanical aspects of the project, such as the 3D design and assembly. All the electronic hardware and software of my rover project was created from scratch, using a completely different approach than the one the original creator of the rover model followed. Most of the hardware component similarities are from elements that were constrained by the existing 3D design (e.g., motors and servomotors) as there was no point in modifying the 3D design if these components were known models that could be easily purchased, as it was the case. The remaining hardware component similarities, such as the motor driver model, are from electronic components that are widely used in similar robotic projects.

After some modifications to the original design, I started 3D printing the model on the summer of 2023. As the rover model was quite large (1/4 scale of a real rover) two entire months were required to 3D print all the pieces, with not many days where the 3D printer was not printing. Between the end of the summer of 2023 and the summer of 2024 I did the assembly of the mechanical parts of the rover and the initial wiring of the motors and servomotors.

As I was developing the mechanical aspects of the rover, I began to realize that the scope of the project was going to be very large and that there would be a lot of hours of work involved. That is when I began to think that this personal project could in fact be converted into the final project of my degree. After validating the project idea with one professor at La Salle URL, I ended up concluding that the hardware and software development parts of the project would be the main focus of my final degree project.

In my previous personal projects, I had frequently used "Arduino" microcontrollers that were very easy to use and met my needs, but for this project, I wanted to learn more about other boards that could also be used in more complex robotic projects, such as the "ESP32", “Teensy”, and "Raspberry Pi" boards. After searching online, I saw that most DIY robotics projects only used a single type of development board, and that is why I decided that for my Mars rover robot, I would try to use several types of development boards, each one of them used in the module of the rover that best takes advantage of their specific characteristics. This would add more educational value to the project, allowing to see each development board optimal usecase, and would differentiate the project from other existing open-source DIY robotic projects.

# 1.2 Objectives

The main objective is to develop an open-source robotic platform build upon the 3D printed model of the Mars rover that was developed as a personal project. The project has been named OpenRover, due to the open-source nature of the platform. This platform will include all the necessary hardware and software to achieve the specific objectives listed below.

As rovers are extremely sophisticated machines, they provide the perfect excuse to build a complex robotic platform that can be continuously expanded by replicating more functionalities that real rovers have.

Other more specific objectives of the project are:

- Control the rover remotely via a custom remote control module with a touchscreen. This module has to be an add-on to an existing generic RC or to a custom RC.
- Create a web dashboard to monitor and control the rover remotely. Self-host the server of this web dashboard on the rover, creating its own WiFi network at startup, and allowing clients to connect and see the dashboard on their browsers. Incorporate a real time camera feed on the web dashboard, showing the view from the rover's head.

- Gather status data so that it can be displayed on the web dashboard and on the screen of the custom remote control.
- Incorporate into the platform a set of functionalities that replicate, at a smaller scale, the functionalities that real Mars rovers have, like a robotic arm, 4-wheel steering or the ability to perform 360º turns.
- Enable anyone who tries building the platform to learn more about the software and hardware aspects of DIY robotic projects, and to have the possibility of adding more software or hardware features to the platform.
- Use different types of development boards among the rover's main functional modules and have interactions between these different development boards. This adds more educational value to the project, allowing to see the optimal usecase for each type of development board. These development boards should be cheap and accessible to the general public.

# 1.3 Project modules overview

The rover has dozens of individual components, both at a hardware and a software level; the objective of this section is not to detail each one of them, but to show the overall picture of the system, with its main modules and components, and the data interactions between the modules.

The 3 main modules of the rover are:

- Central rover module: It has the development board that is inside the main body of the rover and that manages all moving elements (e.g., motors, servomotors) as well as the rover's sensors and sending/receiving the radio signal.
- Remote control and touchscreen module: It has the development board that is responsible for the touchscreen, reading the RC channel values and sending/receiving the radio signal.
- Camera and webserver module: It has the development board that is inside the head of the rover and that is able to use a camera, as well as generating a WiFi and hosting a website.

Each of these modules hasseveral individual components inside, on the diagram shown in Figure 1, only the most important individual components of each module are shown. This diagram is very basic and only meant to facilitate the understanding of each of the module’s purpose and its interactions.

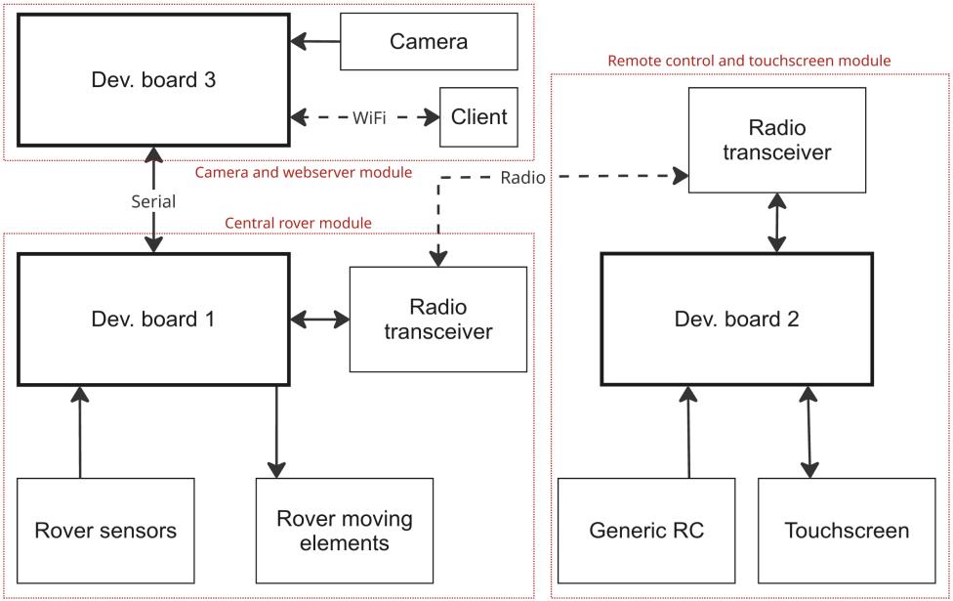
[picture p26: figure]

Figure 1. Modules diagram (own elaboration)

In Figure 1, the dashed arrows indicate wireless communication between the components, and the conventional arrows indicate wired communication. The directionality of the arrows is also important, conceptually indicating the origin and destination of the data that is transmitted. Most of the communication methods employed to connect the different components are not detailed in this diagram, as only an overview of the system is shown at this moment. The exact communication methods and protocols used (e.g., between development board 2 and the touchscreen), will be specified in the analysis section for each component that requires it.

# 1.4 Methodology

Regarding the methodology that has been used to develop this project, we have to differentiate between the theoretical and practical aspects of the project.

The first steps of development were part of the theoretical framework. In this stage, an investigation was conducted on how Mars rovers work and what some of their main functionalities are. This research was carried out to provide some context, since the aim of this project is to use the Mars rover concept simply as an excuse to develop a very complex robot. Therefore, the developed functionalities do not need to faithfully replicate the ones that real Mars rovers have.

Once this initial investigation was conducted, an exploration of existing open-source DIY robotic projects was done, in order to see what new and interesting concepts each one of them contributed (e.g., use of a custom 3D printed RC customized to the robot needs), but also what things did they lack (e.g., only one type of development board was used).

Thanks to this exploration, but also to many completely original ideas not seen in other projects, a list of objectives for the project was created. From these general objectives, a more specific list of requirements was elaborated; these requirements detail the different technical outcomes that are expected, and are very useful to see, at the end of the project, whether each requirement was fulfilled or not. The final part of the theoretical framework consisted in analyzing specific hardware components and software technologies that had the potential of being included in the project.

In the practical framework, from the list of potential components and technologies, some were selected for the design and creation of the project's solution, and arguments are provided to justify why these options were the ones selected. Having selected the hardware components, it was then possible to buy all the necessary hardware components of the project.

With these hardware components at hand, the next step consisted in conducting several experiments using prototyping boards and creating test programs, in order to see the limitations and possible problems of the hardware and software. Once the testing was complete, if necessary, the hardware was soldered on a soldering board. Finally, with all the hardware securely placed and connected, new software functionalities that used the hardware were developed. As the main rover modules are fairly independent, the process described in this paragraph was done on a module-by-module basis, starting with the central rover module, continuing with the RC and touchscreen module, and ending with the camera and webserver module.

Finally, once the technical development was finished, some READMEs were created and the project was made open-source and published on GitHub.

# 2 Requirements definition

From the objectives of the project, the requisites can be defined and categorized into the mechanical, software and hardware aspects of the rover model.

# 2.1 Mechanical structure requirements

Even though the mechanical aspect of the rover model is not fully inside the scope of this final degree project, which focuses more on the hardware and software aspects, it is still interesting to point out some of the requirements that the mechanical platform should fulfill.

- 6-wheel drive platform.
- 4 steerable wheels.
- 4-axis foldable robotic arm with gripper.
- Tiltable and rotary head, with space for a development board and a camera.
- Rocker-bogie mechanism.
- 3D printed structure except the components subjected to high stress or that have common shapes (e.g., tubes).
- All-terrain capabilities, capable of withstanding a lot of mechanical stress.

# 2.2 Hardware requirements

The following list of hardware requirements conceptually details the main hardware components that are required for the rover, as well as some of their more important specifications.

- Custom remote control and touchscreen module that boots almost immediately, to allow a quick an easy operation and monitorization of the robot. The RC has to be able to monitor its battery status. The custom remote control module and screen has to be easily detachable, using wire connectors, allowing to return the generic RC or custom RC to its original form.
- Single battery that powers all the elements of the rover model and that has a good enough discharge rate.
- Radio module that allows bidirectional communication between the rover and the remote control, has low latency and good enough data transmission rate.
- Environmental sensors in the rover model to detect temperature, humidity, pressure and altitude. Battery sensor to monitor the rover's battery status.
- Development board that allows the use of a camera and that has an integrated WiFi module. The board must be able to broadcast a WiFi signal and host a simple website server.

- Motor drivers and motors that allow speed control. Servomotors with a 180º freedom range.
- Development board that can take care of all the real time operations on the rover model (e.g., motor and servomotor control). This board has to boot almost immediately.
- Cable management, especially on the more visible and exposed parts of the model. Use standard wiring connectors to facilitate assembly, disassembly and repairs (e.g., JST connectors).
- All development boards must support some sort of serial communication.

# 2.3 Software requirements

The following list of software requirements details the specific characteristics and functionalities that have to be achieved via software.

- Concurrency support. Both the rover model and its custom remote control have to be able to execute multiple tasks concurrently (e.g., send status data through radio while an automated servomotor movement is being performed).
- Different operation modes have to be implemented. 4 main operation modes can be selected from the RC touchscreen: conventional driving control, 360º turn control, robotic arm control, head control.
- The RC module has to read the generic or custom RC channel values (e.g., via a communication port in a generic RC, or using an ADC to read joystick values in a custom RC) and send a radio signal with these channel values, using the custom communication protocol of the rover. The module has to have at least 8 channels (4 for the joystick axis and 4 for the AUX channels) .
- The RC touchscreen has to be able to display the following status data: rover battery, RC battery, temperature, humidity, pressure, altitude, current RC values being sent, CPU temperature and workload of the board that hosts the website and has the camera, speed, wheel revolutions, traveled distance. For the temperature and humidity, graphs detailing their evolution over the past minute also have to be displayed.
- The RC touchscreen has to display a selection menu to change between the "Home/Control" and "Monitor" screens. These screens will have all the elements described in previous remote control requirements.
- The webserver of the monitoring dashboard, which displays the same status data as the RC touchscreen and the temperature and humidity graphs, must be very lightweight and self-hosted on a development board. The WiFi network and the web server automatically start as soon as the development board is booted. A camera feed panel appears in the web dashboard, and the feed can be started or stopped to save resources. Some type of control element (e.g., joysticks) also should appear in the web dashboard, allowing to manage some of the rover functionalities.

- Implement Ackermann steering equations to avoid tire slipping. With these equations, given a wanted turning radius for the rover, we calculate the optimal steering angle and speed of each wheel.
- Create a custom communication protocol between the development boards that has a low packet size, helping to increase packet transmission rate and improve concurrency. This custom protocol should be the same for radio and wired serial communications, allowing to easily forward to serial a received radio packet and vice versa.
- Implement remote control link loss detection, showing the RC link status on the touchscreen of the remote, and making sounds with a buzzer in the rover if it detects that the signal has been lost. This buzzer also has to make sounds if the rover's battery is low.
- Develop modular code, organizing the implementation of functionalities into separate files, each responsible for a specific aspect of the system.

# 3 Theoretical framework

Prior to being able to implement a solution, a thorough research phase must be done. Among other things, this phase includes research related to the way Mars rovers work and what some of their main functionalities are, as well as deep exploration of different software and hardware technologies that have the potential of being included in the project.

# 3.1 Mars rover definition

Mars rovers are planetary surface exploration robots that space agencies like NASA send to Mars to explore the planet and collect information that is sent back to Earth.

The latest Mars rovers, like the Perseverance [1] model that was sent in 2020, have the main objective of searching for signs of ancient microbial life, exploring the habitability of the planet and collecting geological samples for a potential future pickup mission.

Due to significant delay in the radio signal transmissions between Mars and Earth, rovers tend to have a high degree of autonomy, being able to explore previously designated areas on their own [1] .

Rovers have to endure conditions that are far more challenging than the ones on Earth, as they must be able to withstand high levels of radiation, extreme temperatures, high acceleration, fine dust particles… Once on their voyage or on their final destination, no reparation is possible, so they must be very resilient in order to remain functional for as long as possible.

Six wheeled platforms are often used by rovers to ensure good traction and optimal all-terrain capabilities. Moreover, an innovative and very interesting mechanism, called rocker-bogie [4] , is implemented in many of the rovers to ensure that they are able to climb over most of the obstacles that they may encounter on Mars.

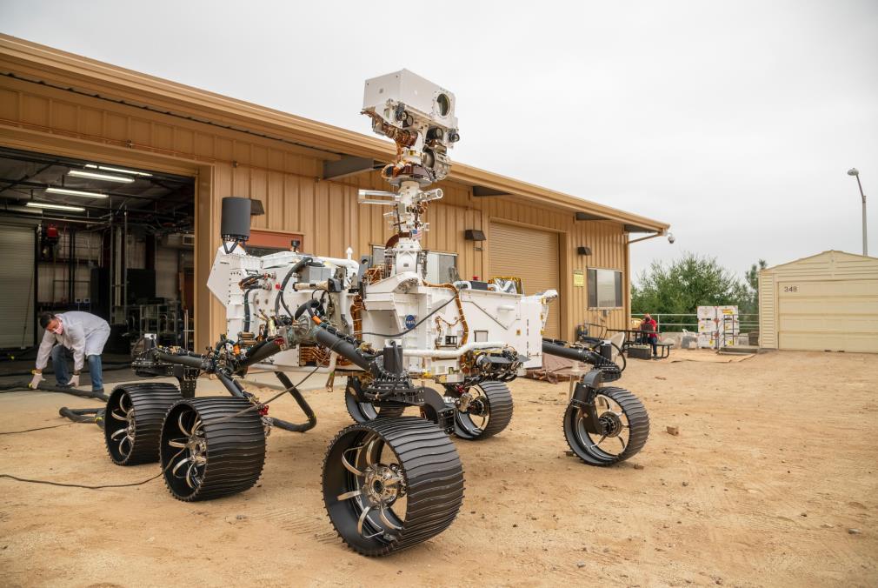
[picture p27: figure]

Figure 2. Perseverance twin rover testing on Earth [2]

## 3.1.1 Components of a Mars rover

In order to provide some context and to replicate some of the functionalities that real Mars rovers have, it is interesting to research what their main components are and what purposes do they serve. The exact components that Mars rovers have differ between models. Focusing on the models sent in the last two expeditions, Curiosity and Perseverance [1] , these are some of the core components that they have:

- Body: Also known as Warm Electronics Box (WEB). It has a rectangular cuboid shape, with a strong and shielded outer layer, that helps protecting the rover’s computer and other electronics that are inside the body.
- Wheels: Six wheels are used for the platform, each of them having their own motor. Only four of the wheels, the two at the front and the two at the back, are steerable. This four-wheel steerable drive enables the rover to make better arcing turns and to have the capability of rotating a full 360 degrees on its center axis. The rover’s wheels are part of the rocker-bogie mechanism, which will be explained in the next section.
- Computing unit: The computing elements are found inside the body. These elements are usually duplicated so that there is always a spare one in case of an error or to compare computing results. These computers tolerate extreme radiation and are responsible for sending commands and data to other components. The computers also help with monitoring the rover’s temperature and power level, as well as storing all the necessary data that is to be sent back to earth when requested.
- Head: On top of the body, there is a mast that holds the rover’s head, which has cameras used for taking pictures of the view from an elevated perspective. It also has other cameras used only for navigation purposes. The head can rotate and tilt to easily change the perspective without needing to move the whole rover.
- Sensors: Several sensors are used to monitor the environmental condition of Mars as well the condition of the computers, electronics, and power of the rover. The MEDA [3] (Mars Environmental Dynamics Analyzer) includes a barometer, humidity sensor, wind sensor and temperature sensors.
- Robotic arm: It is foldable and has several joints, offering flexibility. The tip of the arm has sensors, cameras, and tools to extract geological samples.

## 3.1.2 Rocker-bogie mechanism

One of the key features of the Curiosity and Perseverance Mars rovers, as well as some previous models, is the rocker-bogie mechanism they employ. Replicating this rocker-bogie mechanism was one of the mechanical requirements of the project, so it was interesting to do some research about this mechanism.

Rocker-bogie [4] is a suspension mechanism developed by NASA in 1988 for its rover model Sojourner. Thanks to its capabilities of maintaining stability while traversing rough terrains, this mechanism has been NASA’s favorite and has also been implemented in the more recent rover models like Curiosity and Perseverance. The mechanism is formed by two main components, the rocker and the bogie; each “leg” of the rover has these two components.

The rocker component is connected to the rover’s body and to the other rocker using a differential. These rockers rotate in an opposed manner respective to each other, meaning that when one of the rocker goes up, the other goes down. Each rocker has the bogie component attached to one end and the drive wheel attached to the other end.

The bogie component has a drive wheel attached to each of the ends and has a free pivot point in the middle that connects to an end of the rocker component.

Some of the main advantages of the mechanism are:

- Ability to withstand a tilt of 50 degrees in any direction without overturning.
- Ability to climb over obstacles with vertical heights up to twice of its wheel diameter.
- Thanks to the differential, when one leg climbs an obstacle that is higher than the one the other leg is climbing, the leg climbing this lower obstacle is pressed downwards, ensuring that all the 6 wheels are touching the ground at all times and therefore ensuring traction and control.
- A complex transmission system is unnecessary, as each wheel has its own motor, simplifying the power transfer mechanism.

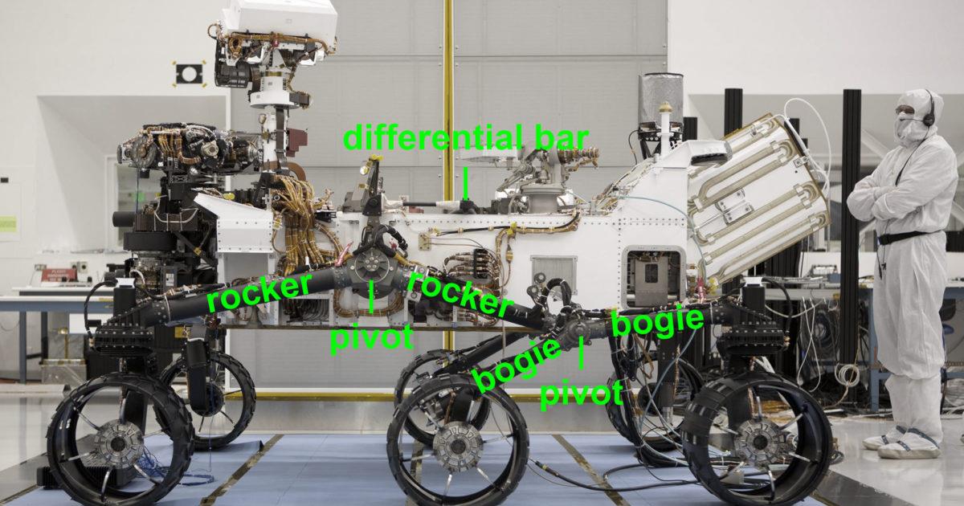
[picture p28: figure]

Figure 3. Rocker-bogie mechanism [5]

## 3.1.3 Ackermann steering

The Ackermann steering geometry [6] [7] is a method of steering that is implemented in almost every vehicle that has steerable wheels, from a common car to a Mars rover, and helps avoid tire slipping. Since implementing Ackermann steering is one of the software requirements of the project, it was interesting to do some research on this subject.

When making a turn, the wheels on the inside of the turn travel a shorter distance than the wheels on the outside, so if we want to avoid tire slipping, the inside wheels have to be placed at a tighter angle. In the case of cars and other common vehicles, we only have to worry about the two steerable wheels, but in Mars rovers we have four steerable wheels, making the steering geometry a bit more complicated.

Focusing on how Ackermann steering works on Mars rovers, there are two issues that need addressing: the direction and the speed of each of the corner wheels. As for the direction, each turning wheels needs to align their center axis towards the desired turning point of the whole rover, as seen in Figure 4.

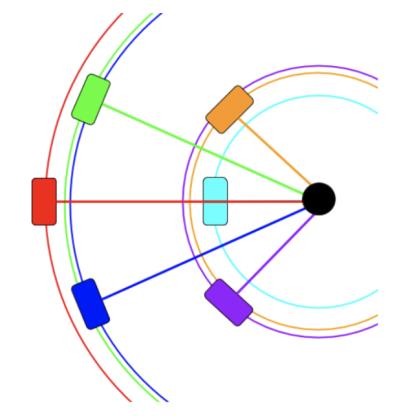
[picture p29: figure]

Figure 4. Ackermann steering turning point [7]

Variables need to be created to represent the different angles, distances and turn radius of the platform. In Figure 5 these variables can be seen.

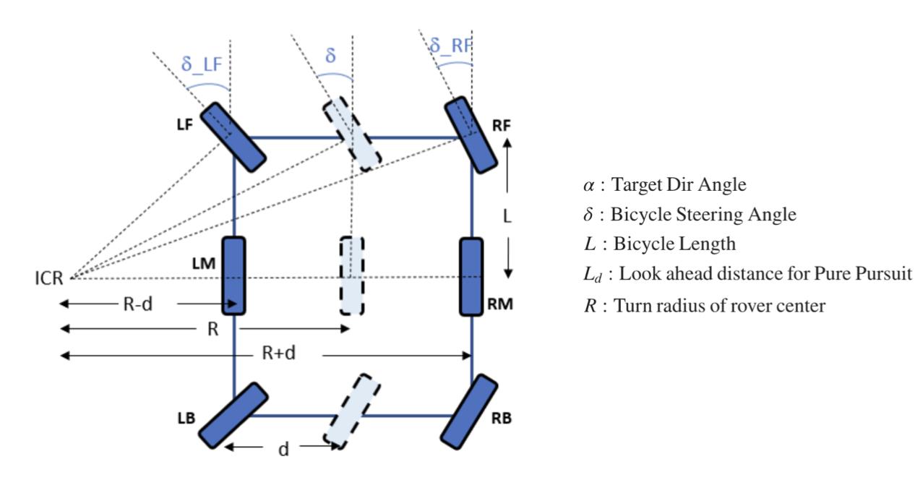
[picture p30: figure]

Figure 5. Ackermann steering rover variables [6]

Given a turning radius and the fixed rover’s dimensions, to calculate the steering angle of each of the wheels some equations are obtained based on the Ackermann steering geometry.

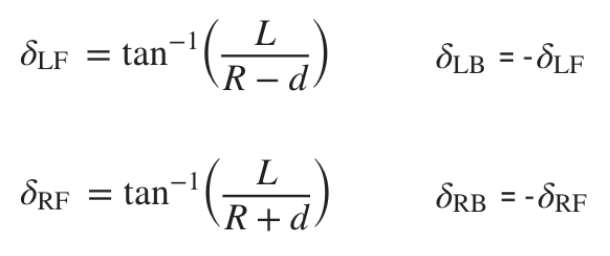
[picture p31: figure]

Where (δLF, δLB, δRF, δLB) are the steering angles for each of the turning wheels. In Figure 5 a term named ICR (Instantaneous Center of Rotation) appears, which indicates the center of the imaginary turning circle of the rover.

As for the speed, since the difference in the speeds of the outer wheels when turning are minimal, given a turning radius and the fixed rover’s dimensions, only three equations are obtained based on the Ackermann steering geometry.

VinnerFrontBackWℎeels | = | Vrover | ∗

( √ L² + (R − d)² )
R + d
VinnerMiddleWℎeel | = | Vrover | ∗

R − d
R + d
| =
VouterWℎeels | | Vrover

Where (VouterWℎeels) is the speed of all the wheels outside the turn, (VinnerMiddleWℎeel) is the speed of the middle wheel inside the turn, (VinnerFrontBackWℎeels) is the speed of the front and back wheels inside the turn and (Vrover) is the speed of the whole rover.

Using these speed equations, assuming a forward right turn at full speed and with a low turning radius, each of the wheel speeds would approximately be:

- Left wheels (LF, LM, LB): 100% speed
- Right-Front and Right-Back wheels (RF, RB): 60% speed
- Right-Middle wheel (RM): 50% speed

As seen in the previous example, the inner wheels will always be slower than the outer wheels. Regarding the angles, the angles of the inner rotating wheels will always be higher than the angles of the outer rotating wheels.

It is also interesting to mention that the distance between the middle wheels of a rover is often a bit larger than the distance between the front or back wheels. This means that a new distance variable would need to be added on Figure 5, and the equations would have to be slightly modified if it was necessary to be very precise. A similar thing happens with the “L” distance, as the distance between the front and middle wheels may be a bit different than the distance between the back and middle wheels. Despite these facts, as the differences in the wheel angles and speeds calculations would be minimal, the explanation of this chapter has been simplified without taking this into account.

All of the equations and images shown in this Ackermann section have been extracted from a sample project on MATLAB’s website [6] and an educational document from NASA’s JPL (Jet Propulsion Laboratory) [7] , with some modifications and improvements to make them clearer. In turn, these two pages have obtained the equations from the original Ackermann steering equations but adapting the original equations to the concept of a Mars rover with a six-wheeled platform and four steerable wheels.

# 3.2 Open-source definition

One of the objectives of the project is to make it open-source [8] , so it is important to research and explain what open-source really means.

Open-source projects are the ones that people can freely modify and share because their inner designs are publicly available and no restrictive licensing is used. Although the term open-source was originally used just for software, nowadays it is a much broader term and it also includes other fields like the more hardware related ones.

Projects where its inner contents (e.g., code, architectural designs…) are not publicly available are called “proprietary” or “closed-source” projects. In these types of projects, often only one individual or organization has access and control over the inner contents, and a very restrictive license is used to ensure that users of the project will not do anything (e.g., modify the project) that the original creators of the project have not expressly permitted.

It is important not to always associate the term open-source with the fact that some project or software is free of charge. The implications of open-source go beyond the economic factor, and there can be open-source projects that require monetary contributions in order to be used, especially if technical support or other similar services are required.

Some of the benefits usually associated with open-source projects[8] , especially software ones, are:

- Control: Experienced users often like to access the code to ensure that it is not doing anything that is not supposed to do (e.g., gathering excessive user data) and to change or improve parts they do not like.
- Security: As anyone can view the source code, these types of projects are considered more secure because vulnerabilities are often quickly identified by the community and fixes are also usually quicker. In lots of cases, the original creators of the project do not have to fix the vulnerabilities themselves, as the community build around the project takes care of this.
- Stability: Many proprietary projects are killed after a few years because they stop being profitable or because the original company that created them was closed. With open-source projects, users can rely on the community to maintain the software long-term, as long as it is deemed useful.
- Community: As stated in many of the previous points, useful or interesting open-source projects are easily able to build a community of developers and users around them. In proprietary projects this community may also exist, but they are usually not able to make contributions to the project, as is the case with open-source projects.

There are several websites to host the projects so that they can be accessible to the rest of the world. One of the most known and used websites for this purpose, especially in the software world, is GitHub [18] . Besides being a platform where users can host their code and other project contents, GitHub allows other users to actively collaborate in the projects; improving the code, reporting bugs and creating new functionalities suggestions. Projects uploaded to GitHub are stored in repositories using Git, which is a Version Control System (VCS). This means that if changes are made to the project files, a “Git commit” can be made to start tracking and managing the changes.

# 3.3 Similar existing projects

Once the project’s general idea was defined, one of the first steps consisted in doing an exhaustive exploration of existing open-source DIY robotic projects, with the aim of identifying the most valuable ideas they offered and the limitations they presented. During this exploration, several projects that developed Mars rover-like platforms were found. Although sharing a common theme, each of these projects had different set of functionalities and a very different approach for developing the robotic platform, mechanical structure, hardware, and software.

The most interesting open-source projects that also developed a Mars rover platform are listed below. For each project, a list of valuable contributions and identified shortcomings is provided.

DIY Mars Perseverance Rover Replica [9]

- Valuable contributions:
- A very detailed, 3D printable, functional and modular design.
- Detailed documentation and videos for mechanical assembly.
- Published design files that allow an easy modification of the 3D printable structure.
- Detailed BOM (Bill Of Materials).
- Shortcomings:
- Very limited functionalities, only basic motor and servomotor functions are implemented.
- Does not have a functional robotic arm.
- Remote control that only uses a generic transmitter and that has no telemetry.
- Low quality camera that uses an analog FPV module as a transmitter.
- Only one type of development board is used (Arduino).
- Poor exterior wire management.

- Inexistent code modulation.
- No sensors.

Jakob Krantz Mars Rover [10]

- Valuable contributions:
- 3D printable functional design.
- Custom 3D printed remote control with an ESP32 that is able to connect via WiFi or LORA to the rover.
- The RC generates an AP where a phone can connect to view telemetry from the Rover on a website.
- GitHub with code and documentation.
- Detailed BOM (Bill Of Materials).
- Sensors for temperature, acceleration and gyroscope.
- Good code modulation.
- 4-axis foldable robotic arm.
- Shortcomings:
- Functional, but not very detailed 3D design.
- No documentation for mechanical assembly.
- Lack of humidity, pressure, and altitude sensors.
- Very basic UI for displaying all the telemetry and camera view. Webserver has very few resources as it is being hosted on an ESP32.
- Instead of having a fixed screen on the RC, there is the need of having a mobile phone screen to display the telemetry and camera view.
- Only one type of development board is used (ESP32).
- Website is hosted on the remote control, which is small and has a tiny battery. This limits the webserver capabilities and the battery life of the RC.
- RC commands are limited by the physical switches and joysticks (no customizable touchscreen for control, which would allow easy expansion of functionalities).

NASA’s JPL Open-Source Rover [11]

- Valuable contributions:
- Sturdy aluminum construction, without 3D printed parts.
- GitHub with code, very detailed documentation, and an assembly manual.
- Detailed BOM (Bill Of Materials).
- RaspberryPi as the rover’s brain, allowing versatility as it is quite powerful.
- Several ways of communication with the robot (Bluetooth, WiFi, Serial…).
- Strong community built around the project, with several people having constructed the rover model and many more making code contributions.
- Use of ROS (Robot Operating System), making the project very educational as it is a very powerful library.

- Shortcomings:
- Functional design, but does not replicate the look of a real rover model.
- Due to the aluminum construction, it ends up being a bit expensive, with an estimated cost of over 1500€.
- Only one type of development board is used (RaspberryPi).
- No mention of a physical RC.
- No camera, although it could be easily added thanks to the RaspberryPi board.
- No robotic arm.
- No sensors.

## 3.3.1 Distinctive characteristics of OpenRover

Having explored and analyzed several of these open-source robotics projects, it was then possible to point out what valuable contributions could differentiate the OpenRover platform developed in this final degree project from other apparently similar robotic projects.

The OpenRover is a complex project that has a broad scope, so only its key distinctive characteristics will be highlighted here:

- Use of different development boards among its main functional modules and interactions between these modules: Many of the explored projects were very complex but only used a single type of developing board, reducing the educational value of the project. By using several development boards that interact with each another, the optimal usecase for each board can be appreciated, and more functionalities can be added.
- Custom Remote Control with touchscreen that is expandable and is not limited by the hardware: Some of the explored projects used a physical RC with switches and joysticks that could easily become obsolete if the project functionalities wanted to be expanded. By adding a touchscreen to the RC, more controls and monitorization parameters can be easily added without the need for more hardware.
- Visually appealing web monitoring dashboard that is self-hosted on the rover and where users can monitor many status parameters of the rover, as well as take a look at the camera feed: Although some of the projects generated websites using development boards like the ESP32, these websites were very basic as they were restricted by the limited resources available in these type of development boards.

For more detailed information about the expected contributions of the project, refer to the Objectives and Requirements definition sections.

# 4 Practical framework

Once the initial research phase was concluded, it was then possible to clearly define how the solution would be implemented. Among other things, this practical phase includes a definition of the solution, with the selected components, and a detailed explanation of all the mechanical, hardware and software work carried out throughout the project.

# 4.1 Solution proposition

As stated in the Objectives section, “The main objective is to develop an open-source robotic platform build upon the 3D printed model of the Mars rover that was developed as a personal project”. Although the mechanical aspect is not fully inside the scope of this final degree project, it is still interesting to mention what resources were used to build the mechanical platform and what additions were made.

The OpenRover’s 3D design of the main mechanical platform originates from the DIY Mars Perseverance Rover Replica [9] project, and the 3D design of the on-board robotic arm originates from the Jakob Krantz Mars Rover [10] project. These two projects are some of the ones listed in the Similar existing projects section of this document, where a list of shortcomings and valuable contributions was made for each of them. Several modifications were made to this original 3D designs, specially to integrate the robotic arm into the main body of the rover. These modifications will be discussed in the Mechanical structure implementation section of the project.

The DIY Mars Perseverance Rover Replica [9] project was selected as the starting point for the 3D design primarily due to its highly detailed, functional, and modular design. Moreover, the original project offered very limited hardware and software capabilities, making the project an interesting foundation to build upon, creating all the hardware and software aspects from scratch.

In the subsections inside this Solution proposition section, the different selected hardware and software components for OpenRover will be detailed and justified. These components are some of the ones presented in the Hardware components analysis and Software technologies and libraries analysis sections, so a more in-detail explanation for each of them can be found in those sections.

## 4.1.1 Selected hardware components

For each hardware category present in the Hardware components analysissection, the selected hardware for OpenRover will be listed. It is important to remember that simpler electronic components categories were not included in the hardware analysis and therefore will also not be included here. In the annexes of this document, there will be a list with most of the components and their cost.

- Development boards: Arduino Mega for rover’s body, controlling all moving elements, sensors, and radio transceiver. ESP32S3 for embedded screen. Arduino Nano for RC PPM value processing and controlling radio transceiver. Raspberry Pi Zero 2W for rover’s head camera and webserver.
- Touchscreen: ESP32S3-8048.

- Camera: RaspberryPi Camera Module 3 Wide.
- Battery: 11.1V LiPo battery with 6000mAh and 50C.
- Wireless communication module: NRF24L01+.
- Environmental sensor: BME280.
- Motors: 12V 30RPM Brushed motors with 11 kgf·cm and 2.2A of current draw. DRV8871 motor driver.
- Servomotors: MG996R/MG995.
- Stepper motor: 12V bipolar stepper with 45 N·cm, 1.5A of current draw and NEMA17. faceplate. A4988 stepper driver.
- Generic remote control: Spektrum DX8.
- Wired communication protocol between development boards: UART.

## 4.1.2 Selected software technologies and libraries

For each software category present in the Software technologies and libraries analysis section, the selected software technologies and libraries for OpenRover will be listed.

- Development environment: PlatformIO IDE with Arduino framework.
- Operating system: Raspberry Pi OS (headless) for the Raspberry Pi Zero 2W board.
- Wireless communication: Arduino RF24 library.
- Wired communication: Arduino SerialTransfer and Python SerialTransfer libraries.
- Touchscreen: Arduino GFX and LVGL libraries. SquareLine Studio platform.
- Camera: Python Picamera2 library.
- Motors: Arduino PalatisSoftPWM library.
- Servomotors: Arduino Servo library.
- Stepper motor: Arduino StepperDriver library.
- Environmental sensor: Adafruit/Arduino BME280 library.
- Generic remote control: Arduino RcTrainer library.
- Website: Flask and Bootstrap.

# 4.2 Hardware and software selection rationale

In this section, the selected hardware, software technologies and libraries will be justified. Comparisons will be made with alternatives listed on the Software technologies and libraries analysis and Hardware components analysis sections, highlighting the advantages and disadvantages of the chosen selection.

## 4.2.1 Hardware components rationale

Development boards

The development board present in the main rover’s body has to be responsible for managing all the moving elements (motors, servomotors, stepper) as well as receiving data from the sensors and using a radio module for communication, among other things. This means that a huge number of pins will be necessary to connect all this hardware. Therefore, the Arduino Mega is an excellent candidate, as it offers 54 digital and 12 analog pins, and was selected as the development board for this module. Another candidate could be the Arduino Due, which has the same amount of pins and comes with higher processing power, but it is a little more easier to maintain and expand, while not posing many limitations for the specific project’s use case.

- Although Express.js is known for being easy to use, Flask offers and even simpler setup process, especially for web applications that do not require sophisticated features.

To complement Flask, which helps with the backend, Bootstrap was selected as a frontend framework. It provides a large set of styled UI components and a responsive grid system, allowing for the quick development of visually appealing and responsive interfaces. This is particularly valuable in a project like OpenRover, as the web dashboard is just one of multiple components. By using Bootstrap, the frontend development time is reduced without sacrificing a clean interface, enabling more focus on other functionalities that are more logic related.

# 4.3 Mechanical structure implementation

To implement the mechanical structure, for each of the rover’s modules the same procedure was followed:

1) 3D designing: Starting from scratch or modifying an existing 3D design, the mechanical components that are going to be 3D printed are designed using apps like Fusion360. In order to do the designs, accurate measurements are taken of other components (e.g., electronic boards, bolts, motors) that will use the 3D printed parts.
2) Slicing: The 3D design of a component is exported to an STL format and is imported into a slicing app like UltiMaker Cura. Depending on the shape of the design, strength needs, and visual appearance wanted, different configuration parameters are set in the slicing app. From the design and configuration parameters, the app generates a GCODE file, which is directly used by 3D printers to print the design. This GCODE file contains the 3D printer extruder’s movements, fan speed, filament flow… for each of the layers.
3) 3D printing: The GCODE file is inputted into the 3D printer using and SD card. The printing bed and extruder are heated up, the filament is fed into the extruder, and the 3D printing process starts, with a very variable duration (from a few minutes to several hours for each 3D printed component, depending on size and quality).
4) Assembly: Using all the 3D printed components and other mechanical components which can be purchased at hardware stores (e.g., PVC tubes, nuts, bolts, aluminum profiles), the rover’s main chassis, head and the RC transmitter cases are assembled.

All the 3D printing and assembly was done in a small at-home workshop, using a consumer-grade 3D printer and common and inexpensive tools that are often used for many DIY projects. Although the exact number of 3D printing hours was not recorded, it is estimated that it took approximately 400 hours to 3D print all the rover’s components. As a matter of a fact, if sample 3D printed pieces used for testing the designs, and final 3D printed pieces that failed mid print were considered, approximately 100 hours would need to be added to the printing hours count.

Since the mechanical aspect of the rover is not fully inside the scope of this final degree project, which puts more focus on the hardware and software aspects, only one image of the modified rover 3D design and of the final 3D printed and assembled mechanical structure will be shown here, without detailing the designing, 3D printing and assembling steps.

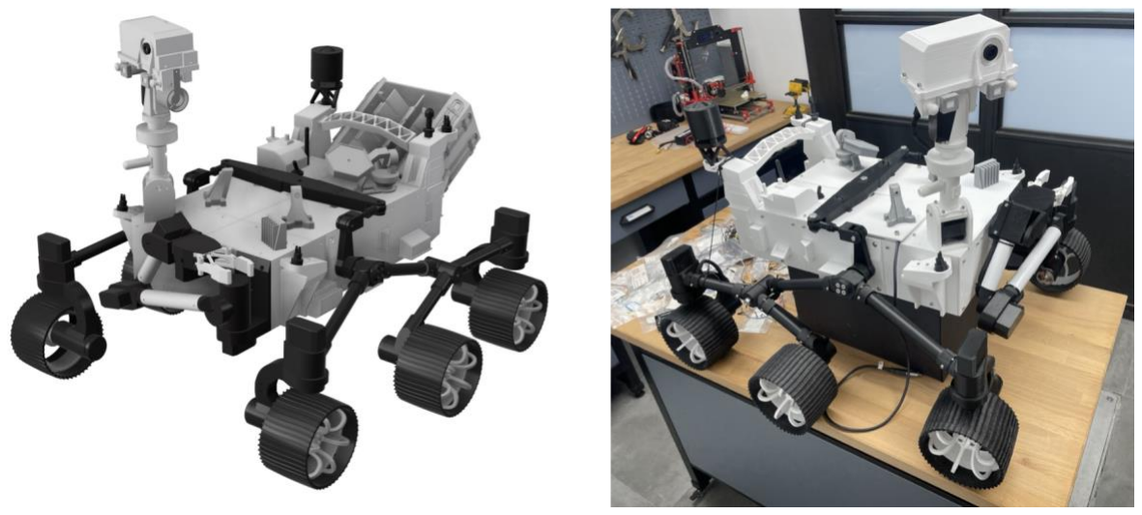
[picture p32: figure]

Figure 6. Rover modified design and assembled mechanical structure (own elaboration of images and original design extracted from [9] )

The original rover’s central mechanical platform design is from the DIY Mars Perseverance Rover Replica [9] . The design shown in Figure 6 is a customized version of this design, with some improvements that are detailed in Annex I.

An explanation of the different designing, 3D printing, and assembling steps of the rover’s mechanical structure is present in Annex I. This explanation is organized on a module-by-module basis and is complemented with several images of the rover’s mechanical platform implementation.

# 4.4 Hardware implementation

This section explains how the selected electronic hardware componentsinteract with each other and describes the process followed to design and create all the custom prototyping PCBs and electrical connections for the rover. The hardware design was made taking into account the specifications defined on the Requirements definition section of the project, with the aim of achieving the desired set of functionalities for the rover.

The implementation of the hardware was done on a module-by-module basis, starting with the central rover module, continuing with the RC and touchscreen module, and ending with the camera and webserver module.

For each of the modules, some initial tests were carried out using prototyping boards and simple connections between the electronic hardware components, usually using DuPont jumper wires. Many of these hardware tests also required software test programs, therefore some of the conducted tests related to hardware will be detailed in the Software implementation section.

The hardware schematics, which detail the components and its connections, will also be shown in this section. Every time a hardware test for a module was successfully completed, prior to disassembling the used prototyping board and/or electrical connections, a design that replicated the used connections was added to the schematics. These schematics could then be used as a guide to create the definitive connections between the components. The components that did not have accessible male/female pin headers, or that required a compact size with close proximity and connections to other components, were soldered onto prototyping PCBs.

## 4.4.1 Central rover module

The hardware present on the central rover module includes an Arduino Mega development board that is responsible for managing all the moving elements (e.g., servomotors, motors, stepper motor), reading the environmental sensor’s values and sending/receiving communications via serial (to/from RaspberryPi Zero board) and via radio (to/from custom RC).

### 4.4.1.1 Schematic

In the schematic seen in Figure 7, all the hardware present on this module can be seen. Besides the components listed in the Selected hardware components section, some other components are present, which have more basic functions but are still important:

- Buck converters: Used to transform the rover’s battery output voltage to a specified lower and more stable voltage level. Essential if only a single battery wants to be used but there are electronic components with different voltage ratings.
- Switches: Allow easy startup/shutdown. Also used to change between operating modes (e.g., debugging/normal mode) and as a travel limit sensor.
- Diode: Ensuresthat current flows only in one direction, protecting from reverse polarity.
- Buzzer: Used to indicate audible alerts.
- Resistors: Used to divide voltages.
- JST connectors: Standard type of Male/Female connectors, used to allow an easy plugging/unplugging and ensuring the correct polarity of the connections.
- Relay: Used as an electronic switch to connect/disconnect power of some of the circuits.


Figure 7. Central rover module schematic (own elaboration)

Schematic component remarks

The single 11.1V LiPo battery of the rover is connected to the input of the main buck converter (SZBK07), which lowers the voltage to 6V. The servomotors are directly connected to this main buck converter output as they need 6V to operate at full power. As most of the other hardware components of the rover work below 6V and receive power from this main buck converter, it has a high current rating of 20A to support the load without overheating. It is also important to mention that the power wires had to be dimensioned to support the required maximum currents, using 22AWG wires (max. 5A) for the motors/servomotors and 14AWG (max. 20A) wires for the input/output of the main buck converter. The only components that do not receive power from the main buck converter are the motor drivers, voltage divider and the buck converter used to power the Arduino, which are directly connected to the 11.1V. The buck converter used to power the Arduino lowers the voltage to 8V, which is within the 7-12V range that the VIN pin, which has an onboard power regulator, supports. Another buck converter is used to lower the voltage from 6V (output of main buck converter) to 5V, as most of the used electronic components are rated to operate at this voltage.

The used 11.1V LiPo battery has three 3.7V cells connected in series. These cells do not stay static at the rated 3.7V, but at a slightly higher/lower voltage value depending on the charge level (4.2V when full, 3.2V when empty). A voltage divider is used to divide the battery’s voltage by three, so that the cell voltage is directly available for reading. As this cell voltage reading will always stay under 4.2V (cell fully charged), it can be read directly using the Arduino ADC, which can read up to a 5V analog value. The combination of the voltage divider and the Arduino’s ADCs acts as a sensor to monitor the battery level, which was one of the hardware requirements.

As the rover’s mechanical platform is quite large, disassembly of some of the parts (e.g., mast with head, rocker-bogie arms with the wheels) from the main body section is necessary to facilitate the rover’s transportation. To easily connect/disconnect the hardware wiring of the different sections, JST connectors with power and control signal wires are used for motors, servomotors, stepper motors and also for the connection between the Arduino and the head’s RaspberryPi Zero 2W board.

For some of the components of the rover, like the servomotors and the RaspberryPi, it is necessary to have the ability to decide via software if they want to be powered or not. Relays are used to implement this functionality, connecting or disconnecting the ground signal of the components on command. They can be set to a Normally Open/Closed (NO/NC) configuration.

### 4.4.1.2 Wiring connections and soldering

Before implementing any electronics inside the rover’s body, the wiring of the chassis was done, with all the wires of the motors and servomotors ending up inside the body. This was a crucial first step, as it laid the foundation for the electrical system and made it possible to perform initial functionality tests on the motors and servomotors. All the chassis wiring was wrapped using a black braided sleeved that help group all the cables and improved overall cable management.


Figure 8. Central rover module chassis wiring (own elaboration)

The next step was soldering all the power-related PCBs. This custom PCBs helped distributing the power from a single battery to a lot of components. In Figure 9, the soldered PCBs that distribute power to the motor drivers and servomotors are shown, along with an image of the custom JST connectors that were soldered to facilitate connections for the motors and servos.


Figure 9. Rover power distribution PCBs (own elaboration)

Once the power distribution boards were completed, they were placed inside the body of the rover, along with the connected motor drivers. Other essential components like buck converters, Arduino Mega, NRF24 radio module and battery were then added in order to start testing, with basic software programs, the motors and servomotors sending remote commands.


Figure 10. Initial rover component connections (own elaboration)

Finally, the remaining hardware components of the central rover module were added, like the environmental sensor, stepper motor, stepper driver and relays. Connections between these components and the existing components were made, mainly using DuPont jumper cables, as many of the newly added components had accessible pin headers. In Figure 11, the final component connections are shown, which are the same ones detailed on Figure 7 schematic.


Figure 11. Final rover component connections (own elaboration)

### 4.4.1.3 Problems and solutions

During the hardware design and implementation of this module, some issues were encountered. Below are some of the key problems and the corresponding solutions that were applied:

- In some cases, while the rover’s battery is disconnected, it is necessary to connect the Arduino development board to a computer via USB for debugging (e.g., reading a sensor’s values and printing them on computer’s serial) or programming purposes. In this scenario, instead of the Arduino receiving power from the battery through the power wires(which are connected to the VIN/GND Arduino pins), it receives power from the USB and outputs some of it via the VIN/GND pins. As this may cause problems, a diode is used to ensure no power is outputted from the VIN pins. Another possible scenario is when all the components, including the Arduino, are receiving power from the battery but we also want to connect the Arduino USB to a computer to debug. In this scenario, an external switch in the VIN pin is used to ensure that, while debugging, the Arduino is being powered by the USB and still has a common ground with the rest of the components, which are being powered up by the battery.
- Most servomotors need to constantly receive PWM signals to maintain their position and behave properly. When the rover’s switch is turned on and power is given to the Arduino Microcontroller and servomotors, there is a lapse of time where the servomotors are receiving power but are not receiving PWM signals, or are receiving erratic signals as the microcontroller is booting up. In some cases, this caused the servos to jitter and to move to random positions during the firsts instants after powering the rover, which posed a problem. For this reason, a relay put on NO (Normally Open) was used to connect/disconnect the servomotors from the power source, ensuring that they were only connected when the microcontroller was ready and sent a signal to the relay.

## 4.4.2 Remote control and touchscreen module

The hardware present on the remote control and touchscreen module includes an ESP32S3 development board that is responsible for managing the screen and an Arduino Nano board that helps processing the RC PPM signals and controlling the radio transceiver. The generic RC unit, on which the custom radio and touchscreen module are mounted, can also be considered a hardware component. However, the only modification made to it involves adapting and utilizing its internal battery to power the custom module.

### 4.4.2.1 Schematic

In the schematic seen in Figure 12, all the hardware present on this module can be seen. Besides the components listed in the Selected hardware components section, some other components are present, which have more basic functions but are still important. As some of these other components were explained on the previous central rover module, here they will only be listed:

- Buck converter.
- Switch.
- Diode.
- Buzzer.
- Resistors.

- JST connectors.
- 3.5mm Jack: Used to connect to the trainer port of the generic transmitter.
- Level shifter: Used to convert signals from one voltage level to another, allowing devices with different operating voltages (e.g., 3.3V and 5V) to communicate with each other.


Figure 12. Remote control and touchscreen module schematic (own elaboration)

Schematic component remarks

In the schematic shown in Figure 12, the generic Spektrum DX8 RC does not appear as an entity, as the only interactions with the developed custom module are through the trainer port, represented in the schematic by the 3.5mm jack that connects to the port, and the shared battery, whose voltage output is also represented in the schematic.

The Spektrum DX8 RC has an internal 7.4V Li-Ion battery [42] . This battery is directly connected to the only buck converter of the custom module, which lowers the voltage to 5V. The only component that is powered directly by the battery’s 7.4V is the Arduino Nano, as it has a voltage regulator with an input range of 7-12V in the VIN pin.

The used 7.4V Li-Ion battery has two 3.7V cells connected in series and behaves similarly to a LiPo battery [36] . As it was the case with the rover’s LiPo battery, this Li-Ion battery cells do no stay static at the rated 3.7V, but at a slightly higher/lower voltage depending on the battery level. A voltage divider is used to divide the battery’s voltage by two, so that the cell voltage can be read. The combination of the Arduino’s ADCs and the voltage divider acts as a battery level sensor, which was one of the hardware requirements for the custom RC.

In the schematic, an ESP32S3 SoC does not appear as an entity, as it is integrated in the same package as the touchscreen. Instead of showing all the typical pins of an ESP32S3, only the available pins that are not used to run the touchscreen are shown. The touchscreen came with some pre-soldered JST connectors for easy interfacing with the available GPIO pins.

There are two diodes in the custom RC module. One diode is used simply as a reverse-polarity safety feature to protect the trainer port connection with the Spektrum DX8 RC. The other diode is used to ensure that when the ESP32S3-8048 board is being powered by the USB, no voltage is outputted from the 5V pin of the board, as it is directly connected to the output of the buck converter (which should not receive voltage).

The level shifter is used for serial communication between the Arduino Nano, which has 5V logic, and the ESP32S3, which has 3.3V logic. The LV (low voltage) and HV (high voltage) reference pins of the level shifter board are directly connected to the 3.3V and 5V pins of the ESP32S3 and the Arduino, respectively. This ensures that the voltage reference values are the same as the ones the boards use.

Although the schematic showcases all the components together, in the physical implementation they are divided into two sections: the touchscreen section and the radio control section. The touchscreen section is only formed by the ESP32S3-8048, and the radio controlsection is formed by the rest of components. These sections are part of the same “Remote control and touchscreen module” and are interconnected using JST connectors with power and data wires. The physical separation of the sections can be seen in Figure 54.

### 4.4.2.2 Wiring connections and soldering

One of the first steps of the RC and touchscreen module implementation was creating all the necessary connections between the hardware components on a prototyping board, as seen in the central image of Figure 13. This way, it was possible to do various tests to check if the hardware design would work prior to soldering the components and creating the definitive connections between them. Additionally, for this first step, a second connector was soldered to the internal battery of the Spektrum DX8 RC, allowing the battery to power both the Spektrum RC and the custom developed RC and touchscreen module. Creating this second connector early in the process was essential to verify whether the internal battery could supply enough current to power everything, and to confirm that the PPM signal could be accurately read with both the Spektrum RC and the custom module sharing the same power source. To validate the correct functioning of the NRF24L01 radio module that was on the prototyping board, a second prototyping board with another Arduino Nano and NRF24L01 was used to carry out some tests. This second prototyping board, whose design is not present in the Figure 12 schematic as it was created only for testing purposes, can be seen on the rightmost image of Figure 13.


Figure 13. Remote control and touchscreen prototyping board (own elaboration)

Once the correct functioning of the hardware was validated and the final schematic was created, a prototyping PCB that would be used to solder all the components except the screen was cut to size. This custom created PCB can be seen in Figure 14. For the remote control and touchscreen module, it was important to have as many connections made with soldering as possible. These types of connections take up less space and are more resistant to movements, which is a big advantage considering that the custom RC module must be very compact and will be subject to a lot of movements while it is being used and handled.


Figure 14. Remote control custom PCB (own elaboration)

The only soldering that had to be done to the touchscreen module was related to creating the custom JST connectors with the appropriate wire length to connect the touchscreen, which is at the front of the Spektrum RC, with the custom remote control PCB which is at the back. In Figure 54, the connection between these two sections can be seen, as well as how the final result of the whole module looks like when the 3D printed cases are used.

### 4.4.2.3 Problems and solutions

During the hardware design and implementation of this module, some issues were encountered. Initially, this module’s design did not include the Arduino Nano board, as all the components were supposed to be connected directly to the ESP32S3 board, which on paper is capable of handling all of them. The touchscreen used up nearly all the ESP32S3 GPIOs, leaving only five free. However, eight available GPIOs were required for all the module’s functionalities (five for NRF24 handling, one for PPM signal reading, one for battery level reading and one for the buzzer). As the ESP32S3 could not accommodate all these inputs and outputs, a solution to the problem was found, which consisted in using an additional Arduino Nano board to handle all I/O-related tasks. This Arduino Nano would bidirectionally communicate with the ESP32S3 via the serial interface, resolving the GPIO number limitation and offloading I/O responsibilities.

## 4.4.3 Camera and webserver module

The hardware present on the camera and webserver module includes a RaspberryPi Zero 2W board that is responsible for receiving camera input, creating a WiFi network with a self-hosted website available in it and sending/receiving communications via serial (to/from Arduino Mega).

### 4.4.3.1 Schematic

In the schematic seen in Figure 15, all the hardware present on this module is shown. Besides the components listed in the Selected hardware components section, some other components are present, which have more basic functions but are still important:

- USB HUB HAT [89] : Connects to RaspberryPi Zero’s Pogo pinsto extend the single micro-USB of the board to four functional USB A ports.
- USB to TTL [90] : Helps connecting devices with TTL logic levels, like microcontrollers, with PCs or other devices that use USB, enabling data communication between them.

- Fans: Used for active cooling, reducing the RaspberryPi’s CPU temperature.


Figure 15. Camera and webserver module schematic (own elaboration)

Schematic component remarks

The four-pin female JST connector that is shown in Figure 15 is connected directly to the four-pin male JST connector that is present in the central rover module. Using this connection, the camera and webserver module receives 5V power and can bidirectionally communicate with the Arduino Mega of the central rover module via serial.

For the serial communication, a USB to TTL converter is used to connect a USB interface of the Raspberry Pi Zero to one of the TX/RX serial interfaces of the Arduino Mega. This converter is necessary because USB and TTL serial (UART, TX/RX) are different standards. Instead of using this converter, the TX/RX pins of the Arduino Mega could be directly connected to the RX/TX pins that are available on the RaspberryPi Zero, but this approach is usually less optimal. One of the reasons behind this isthat the voltage levels of the RaspberryPi and the Arduino are different (3.3V and 5V respectively) so an additional “level shifter” board would also be needed. Another reason is that there is only one TX/RX interface available on the RaspberryPi Zero, whereas multiple USBs can be available if a USB Hub is used, making it possible to have several communication interfaces.

The RaspberryPi Zero board only features a single micro-USB port, but it includes some pads at the bottom side that expose the D+ and D- USB connections. These allow for the connection of USB Hub boards, which expand the number of available USB ports. These USB Hubs come in various formats, with some designed to match the RaspberryPi Zero form factor, offering an integrated and compact solution for expanding USBs. This is the case of the selected USB HUB HAT for the project, which sits beneath the RaspberryPi and adds four USB-A ports. HAT stands for “Hardware Attached on Top”, which means that the board is an add-on for a specific RaspberryPi model and easily connects to the GPIO or bottom pads layout of the board. This USB HUB HAT is essential to the project since USB to TTL converters generally use USB-A rather than micro-USB. Additionally, it provides flexibility to connect other USB peripherals to the RaspberryPi Zero, such as USB memory sticks or USB antennas to increase WiFi range.

As the selected camera is fully compatible with the Zero board, a FFC (Flat Flexible Cable) is used to directly connect the camera to the RaspberryPi Zero board.

### 4.4.3.2 Wiring connections and soldering

The wiring connections and soldering for this module were rather straightforward, as little soldering was needed and there were not many connections between the components. That said, the main challenge was managing the limited space available; wires had to be cut to precise lengths to minimize clutter and the components needed to be distributed following an optimal layout. The first steps of the module’s wiring process consisted in connecting the FFC between the camera and the RaspberryPi board, coupling the USB HUB HAT to the board using its Pogo pins, and connecting RX/TX from the JST connector to RX/TX of the USB to TTL converter. This process is shown in Figure 16.


Figure 16. Initial camera and webserver module connections (own elaboration)

Once these initial connections were made, the USB to TTL was plugged into one of the ports of the USB HUB HAT and both the fans and the RaspberryPi board were connected to the 5V power source that the JST connector provided. All the definitive connections are shown in Figure 17.


Figure 17. Final camera and webserver module connections (own elaboration)

In Figure 56, more images of the component’s placement and wiring can be seen.

### 4.4.3.3 Problems and solutions

During the implementation of this module, some issues were encountered. When the RaspberryPi Zero was powered up and the first testing programs were executed, after some time the performance of the board started to decrease. Doing some research on the internet
[91] and conducting testsrunning programs with different processor needs, it was clear that this performance decline was caused by the CPU reaching its maximum temperature, which caused the board to throttle down. To solve this problem, a heatsink was added for passive cooling and two fans were added for active cooling, ensuring that the CPU did not reach its maximum temperature no matter the load.

# 4.5 Software implementation

This section explains how, using the selected software technologies and libraries, the different software modules of the OpenRover project were implemented, and how they interact with each other. The software design was made considering the specifications defined on the Requirements definition section of the project, with the aim of achieving the desired set of functionalities for the rover.

As the project modules are fairly independent, the implementation of the software was also done on a module-by-module basis, starting with the central rover module, continuing with the RC and touchscreen module, and ending with the camera and webserver module.

The codebase of the project is very large, and it would be impossible to show and explain each of the implemented individual functions in this document. Instead, diagrams are presented to illustrate the flow of the different programs, what files are they composed of and the interactions between these files.

One of the requirements of the OpenRover project was having a modular software design, organizing the implementation of functionalities into separate files, each responsible for a specific aspect of the system. This was considered for the software development of all modules.

The main programming languages used for the modules are C++ and Python. Many of the used libraries follow OOP (Object-oriented programming), requiring the creation of objects to access their functionalities, but most of the code written for the modules does not follow OOP. For the camera and webserver module, HTML, CSS and JavaScript are also used.

Since the bulk of the code does not follow OOP, class diagrams illustrating all the classes and their relations would not be the best option. Instead, diagrams detailing the created files are presented. In the case of C++, all the created header (.h), which have the functions headers that other files can call, and implementation (.cpp) files, are presented. In the case of Python, all the “.py” files, which include function headers and implementation, are presented. The diagrams also illustrate the relations between these files, indicating which files invoke functions from other files. Each of the “.cpp” and “.py” files implement the functions that are responsible for a specific aspect of the system (e.g., serial communication, managing motors, radio communication). In the case of C++, each “.cpp” file usually includes a “.h” file with the same name, which has the headers of functions present in the “.cpp” that can be invoked from other files that include this “.h” file.

## 4.5.1 Central rover module

The software present in the central rover module is responsible for controlling all the moving elements (e.g., servomotors), reading the environmental sensor’s values, sending/receiving communications via serial and via radio and implementing the logic for many of the rover’s functionalities (e.g., controlling robotic arm, 360º turn control), among other things.

The software of this module has been developed using C++ and PlatformIO IDE [14] . All the code has been designed to run and has been tested on an Arduino Mega microcontroller board.

### 4.5.1.1 Program structure

In Figure 18, a diagram detailing the most important created files for the module and its relations is shown. The function headers present in these files are also detailed in this diagram. For the function implementation files (.cpp), only the headers of the internal use functions are detailed, which are not present in the header files (.h) with the same names as the “.cpp” files. Internal use functions are all those functions which cannot be invoked from other files, as their purpose is to implement parts of the logic behind the functions present in the header files.


Figure 18. Key header and implementation files for central rover module (own elaboration)

Each developed “.cpp” file implements functions dedicated to a specific aspect of the system. Below is a description of the main responsibilities assigned to each of these files:

- armServoManager.cpp: Facilitates the control of the robotic arm servomotors, modifying the angles at a constant speed depending on joysticks positions. Makes sure that the angles of each of the axis are within the limits.
- batteryManager.cpp: Implements calculations to convert the read analog values from the voltage divider to numeric cell voltage and percentage values.
- buzzerManager.cpp: Provides a set of buzzes with different tones and durations.
- headMovementsManager.cpp: Facilitates the control of the head’s stepper motor and servomotor, modifying the pan and tilt angles at a constant speed depending on joystick positions. Makes sure that the pan and tilt angles are within the limits. Initializes the stepper’s home position by reading a limit switch that indicates the maximum pan angle.
- motorManager.cpp: Facilitates the control of the wheel motors, modifying the individual speed and direction depending on joystick positions and selected operation mode. Implements Ackermann steering calculations to adjust each speed depending on the desired turning radius.
- opModeManager.cpp: Facilitates the change of the current operation mode and calls required procedures at the appropriate intervals, depending on operation mode.
- radioCommunication.cpp: Facilitates receiving and sending custom frames via radio.
- rcValuesManager.cpp: Provides information of the joysticks position, translating received joystick numeric values to known positions (e.g., up, down, centered). Implements calculations to detect if the remote-control link is lost.
- receivedFramesHandling.cpp: Handles the operations that need to be done for each type of received radio or serial frame.
- relayManager.cpp: Simplifies the state selection (on/off) of all the relays.
- sensorsManager.cpp: Facilitates the reading of sensor’s values, like the BME280’s values.
- serialCommunication.cpp: Facilitates receiving and sending custom frames via serial.
- statusDataManager.cpp: Facilitates the retrieval of status data (e.g., environmental sensors, battery values) at the appropriate intervals. Implements calculations to detect if the serial link with the RaspberryPi is lost, indicating that it probably has shut down.
- valuesFromFrameConversion.cpp: Translates the frames of the custom communication protocol to known data structures, which are more easily used.

- valuesToFrameConversion.cpp: Translates known data structures to frames of the custom communication protocol, which are optimized for data transfer.
- wheelServoManager.cpp: Facilitates the control of the wheel’s turn servomotors, modifying the angles at a constant speed depending on joysticks positions. Makes sure that the angles of wheel are within the limits. Implements Ackermann steering calculations to adjust each wheel’s angle depending on the desired rover turning radius.

The “main.cpp” file does not contain any complex logic; its primary responsibility is handling the initial setup and making recurring calls to functions defined in the developed header files. This approach aligns with the requirement of using a modular software design.

Several of the function headers shown in Figure 18 utilize custom data structures. These structures facilitate the storage, transfer, and manipulation of data throughout the different parts of the system. All the structures used in this module are defined on a header file, which is included by the files that require them. In Figure 19, these custom structures are detailed.


Figure 19. Central rover module data structures (own elaboration)

The structure names are self-explanatory, with the exception of the “Frame” structure, which would require a deeper explanation. This structure is integral to the custom communication protocol used to communicate between the OpenRover’s modules. Later in the document, a dedicated Communication protocol section will provide an explanation for this structure and the communication protocol.
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

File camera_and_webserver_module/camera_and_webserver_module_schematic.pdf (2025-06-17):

Pin Headers; SDA1 5V SCL1 GND; GPIO4 TX; GND RX; GPIO17 GPIO18 GPIO27 GND; GPIO22 GPIO23; 3V3 GPIO24 MOSI GND; MISO GPIO25; SCLK GPIO8 GND GPIO7; ID_SD GPIO5; GPIO6; GPIO13; GPIO19; GPIO26; GND; ID_SC GND; GPIO12 GND; GPIO16; GPIO20 GPIO21; RASPBERRY PI ZERO 2W; FFC Connector; USB HUB HAT; Usb_1; Usb_2; Usb_3; Usb_4; JST4-F FAN 1; FAN 2; FFC Cable; RPI CAMERA; USB TO TTL; Pogo pin connectors; 5V GND D+ D-; RX_RPI; TX_RPI; 5V GND RX TX 3V3; RX_RPI TX_RPI; 5V_RPI; 5V GND D+ D- Pogo pin connectors

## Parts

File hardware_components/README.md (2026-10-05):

## Hardware components

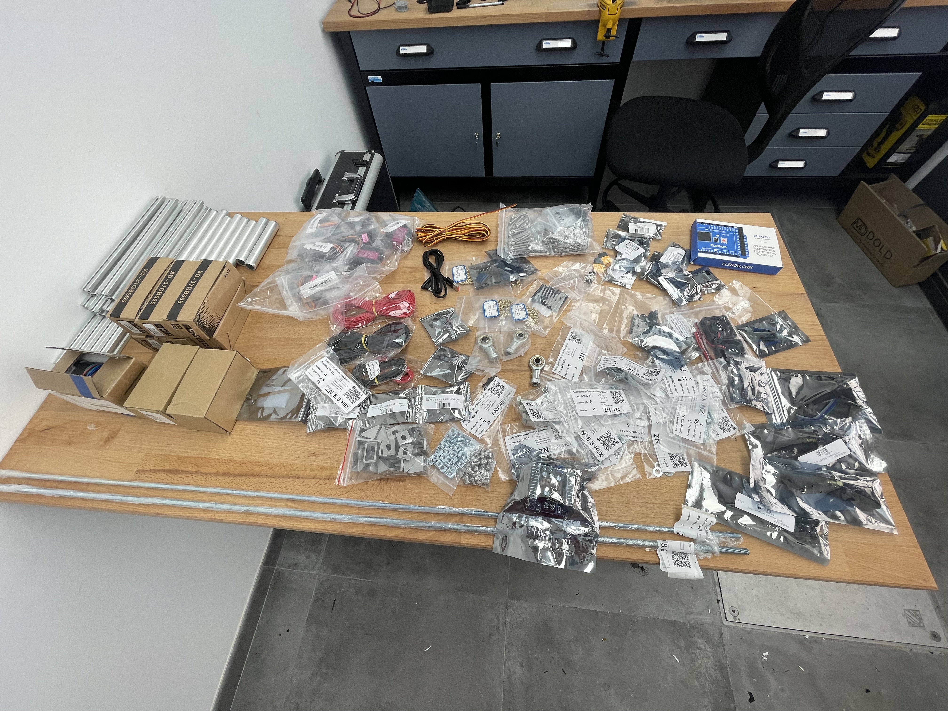
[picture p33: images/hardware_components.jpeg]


Most important hardware components needed for the rover:

- NEMA17 stepper motor (x1)
- Toggle switch 20A (x1)
- SS-12D10 switch (x1)
- Arduino Mega (x1)
- MG996R/DS3225 servo (x10)
- XD-37GB555 motor (x6)
- NRF24L01 transceiver module (x1)
- NRF24L01 3.3V regulator (x1)
- XT60 connector female and male (x1)
- DRV8871 motor driver (x6)
- SZBK07 buck converter 20A (x1)
- 22AWG wire 20 meters red and 20 meters black (x1)
- 14AWG wire 1 meter red and 1 meter black (x1)
- Servo extension cable 22AWG 5 meters (x1)
- Dupont jumper wires (as needed)
- BME280 sensor (x1)
- 12V 4010 fan (x2)
- A4988 stepper motor driver (x1)
- Matte Black vinyl wrap (as needed)
- Self closing braided sleeve for wires (as needed)
- JST-XH male and female connectors (as needed)
- Micro limit switch with roller (x1)
- 6000mAh 11.1V 50C LiPo battery (x1)
- XL4015 buck converter 5A (x2)
- RaspberryPi Zero 2W (x1)
- RaspberryPi Cam V3 Wide (x1)
- FFC cable 15 centimeters for PiZero and PiCam (x1)
- Heatsink for PiZero (x1)
- CP2102 USB to TTL converter (x1)
- 4-USB HAT for PiZero (x1)
- 1N5817 Schottky diode (x1)
- Prototyping boards (as needed)
- Buzzer (x1)
- HW482 relay (x2)
- 100uF electrolytic capacitator (x1)
- 1k ohm resistor (x1), 2k ohm resistor (x1) 

Most important hardware components needed for first remote control option (custom RC PCB):
- Buzzer (x1)
- ESP32S3_8048S043 IPS touchscreen (x1)
- 5-pin JST-XH male and female connectors (x1)
- Spiral plastic sleeve for wires (as needed)
- JH-D202X joystick (x2)
- Arduino Nano (x1)
- NRF24L01 transceiver module (x1)
- NRF24L01 3.3V regulator (x1)
- Colored wires (as needed)
- SS-12D10 switch (x1)
- Toggle switch 20A (x2)
- Push button (x1)
- 4-channel logic level converter (x1)
- 100 ohm resistors (x1), 1k ohm resistors (x2)
- Double AAA battery holder (x2)
- Rechargeable AAA 1.2V 750mAh NiMH battery (x4)
- Manufactured double-layer PCB (x1)

Most important hardware components needed for second remote control option (attachment for a generic/commercial RC)
- Buzzer (x1)
- ESP32S3_8048S043 IPS touchscreen (x1)
- Spiral plastic sleeve for wires (as needed)
- Arduino Nano (x1)
- NRF24L01 transceiver module (x1)
- NRF24L01 3.3V regulator (x1)
- Colored wires (as needed)
- SS-12D10 switch (x1)
- 4-channel logic level converter (x1)
- Jack 3.5mm mono connector (x1)
- Mini buck converter 2A (x1)
- Prototyping boards (as needed)
- 1N5817 Schottky diode (x2)
- 5-pin JST-XH male and female connectors (x1), 2-pin JST male connector (x1)
- 1k ohm resistor (x2)

These hardware components were purchased on Aliexpress, but most of them are also available on Amazon.

For the mechanical platform, a parts list is provided in the [original project used for the mechanical design](https://howtomechatronics.com/projects/diy-mars-perseverance-rover-replica-with-arduino/). An [extended version of the mechanical parts list](/hardware_components/mechanical_parts_list.txt) is also provided in this ``hardware_components/`` folder, which includes the remote controller's parts.

### Cost
This is the estimated cost of all the mechanical and hardware components: 

-For the rover, around 900€

-For the first remote control option (custom RC PCB), around 120€

-For the second remote control option (attachment for a generic/commercial RC), around 40€ (not including the generic/commercial RC)

This cost does not include the tools that are necessary to build the rover and remote controller (e.g., soldering iron, power supply for tests, multimeter).

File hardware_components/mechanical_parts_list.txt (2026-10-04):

*Extracted from HowToMechatronics (https://howtomechatronics.com/projects/diy-mars-perseverance-rover-replica-with-arduino/). This list has been updated with some additional mechanical parts (for both the rover and the custom remote controller). 

----- ROVER PARTS -----
Bolts and nuts:
M3 x 8mm - 100
M3 x 10mm - 60
M3 x 12mm - 50
M3 x 16mm - 60
M3 x 20mm - 20
M3 x 35mm - 5
M3 x 40mm - 5
M4 x 25mm - 10
M5 x 30mm - 5
M4 x 30mm - 10
M4 x 20mm Flat socket head - 35
M6 x 55mm - 4
M6 nuts self-locking - 4
M6 washers - 4
M8 x 30mm - 2
M8 x 60mm - 1
M8 x 70mm - 2
M8 x 90/95mm - 2
M8 nuts - 4
M8 nuts self-locking - 3
M8 washers - 5
Grub Screw M3 x 6mm - 14

Bearings:
608RS - 8x22x7mm - 8
626RS - 6x19x6mm - 8
625RS - 5x16x5mm - 4

Other parts:
M8 Female Rod End Ball Joint - 2
Threaded rod M8 x 50mm length - 2
Threaded rod M6 x 75mm
T-Slot corner brackets - 16
T-Slot Nuts: M3 - 100;  M5 - 50
M5 washers - 50 for the corner brackets

Metal servo horn/arm with round/disk shape - 12
M3 threaded insert - 100 (approximate)
M4 threaded insert - 30 (approximate)
Neodymium magnets - 8x2mm - 10

Aluminum 20mm tube - see rover 3D design for quantity and lengths
Aluminum or PVC 25mm tube - see rover's robotic arm 3D design for quantity and lengths
T-slot aluminum profile 20x20mm - see rover 3D design for quantity and lengths

----- FIRST REMOTE CONTROL OPTION (CUSTOM REMOTE CONTROL PCB) PARTS -----
Bolts:
M3 x 8mm - 6 - preferably with flattened head (ISO-7380)
M3 x 10mm - 4 - preferably with flattened head (ISO-7380)
M3 x 12mm - 4
M3 x 16mm - 1

Other parts:
M3 threaded insert - 20 (approximate)

Laser/CNC cut top and bottom acrylic plate - 3mm thick - see 2D .dxf designs inside the "remote_control_and_touchscreen_module/pcb_remote_control/" folder

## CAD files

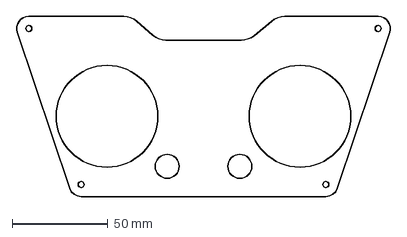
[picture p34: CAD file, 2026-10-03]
remote_control_and_touchscreen_module/pcb_remote_control/rc_top_plate.dxf
195.2 x 93.9 mm

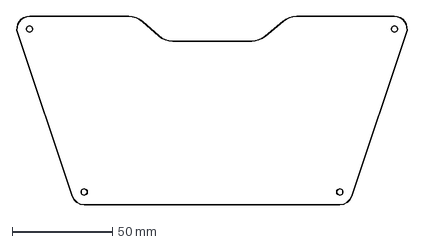
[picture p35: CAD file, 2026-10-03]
remote_control_and_touchscreen_module/pcb_remote_control/rc_bottom_plate.dxf
195.2 x 93.9 mm

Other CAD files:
3d_designs/rc-pcb-spacers-and-touchscreen-case.f3d
3d_designs/rc_and_touchscreen_cases-spektrum_dx8.f3d
3d_designs/rover_modified_and_new_parts.f3d

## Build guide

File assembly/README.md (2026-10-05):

# Hardware and mechanical assembly

A detailed guide for the mechanical assembly process is available in the [original project used for the mechanical design](https://howtomechatronics.com/projects/diy-mars-perseverance-rover-replica-with-arduino/). 

For the hardware assembly, for each of the OpenRover's modules ([central rover](/central_rover_module/), [remote control and touchscreen](/remote_control_and_touchscreen_module/), and [camera and webserver](/camera_and_webserver_module/)), schematics of the wiring connections are provided. 

Additionally, some images that detail the hardware and mechanical assembly process will be shown here. 

## Rover assembly process

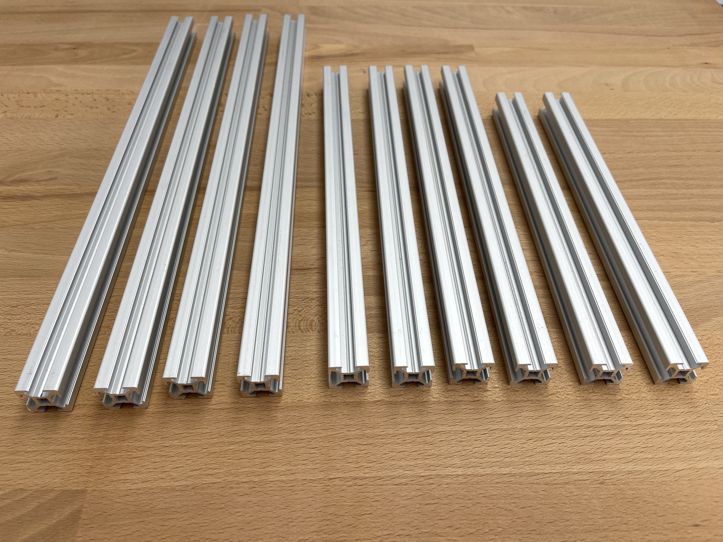
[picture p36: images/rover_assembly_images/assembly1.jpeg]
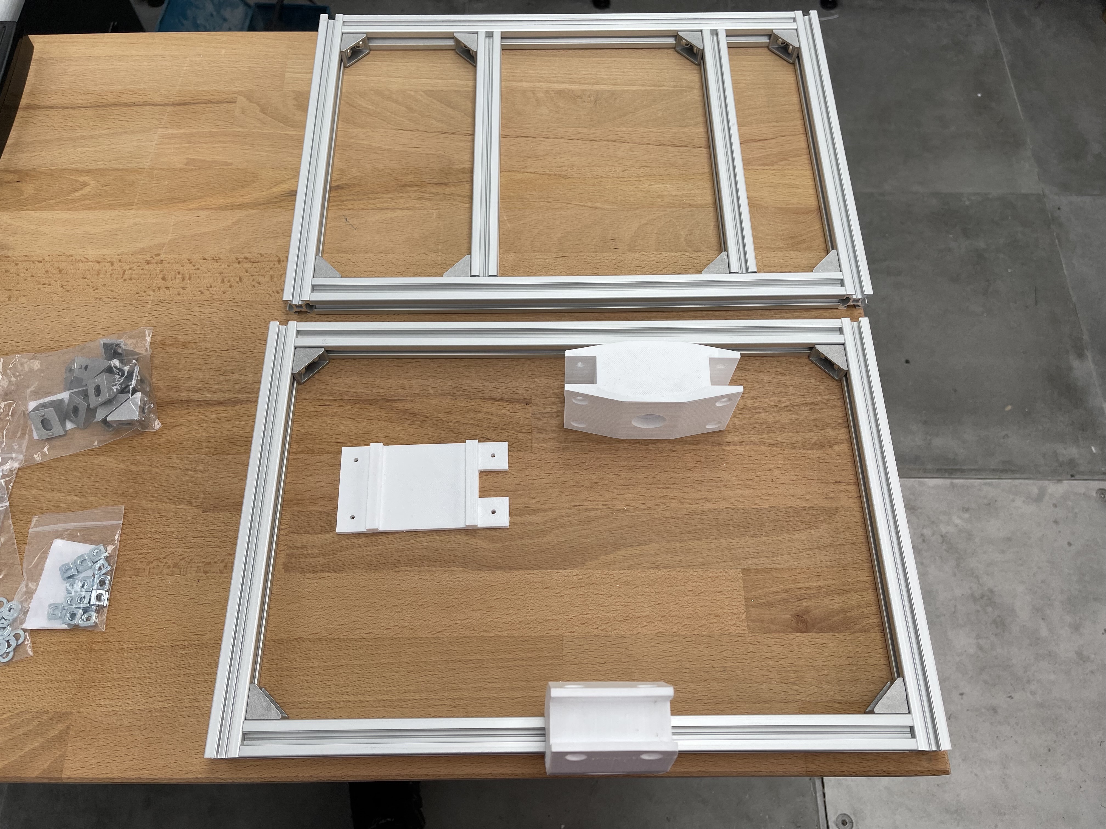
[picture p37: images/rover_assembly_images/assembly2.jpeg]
|  |  |
| --- | --- |
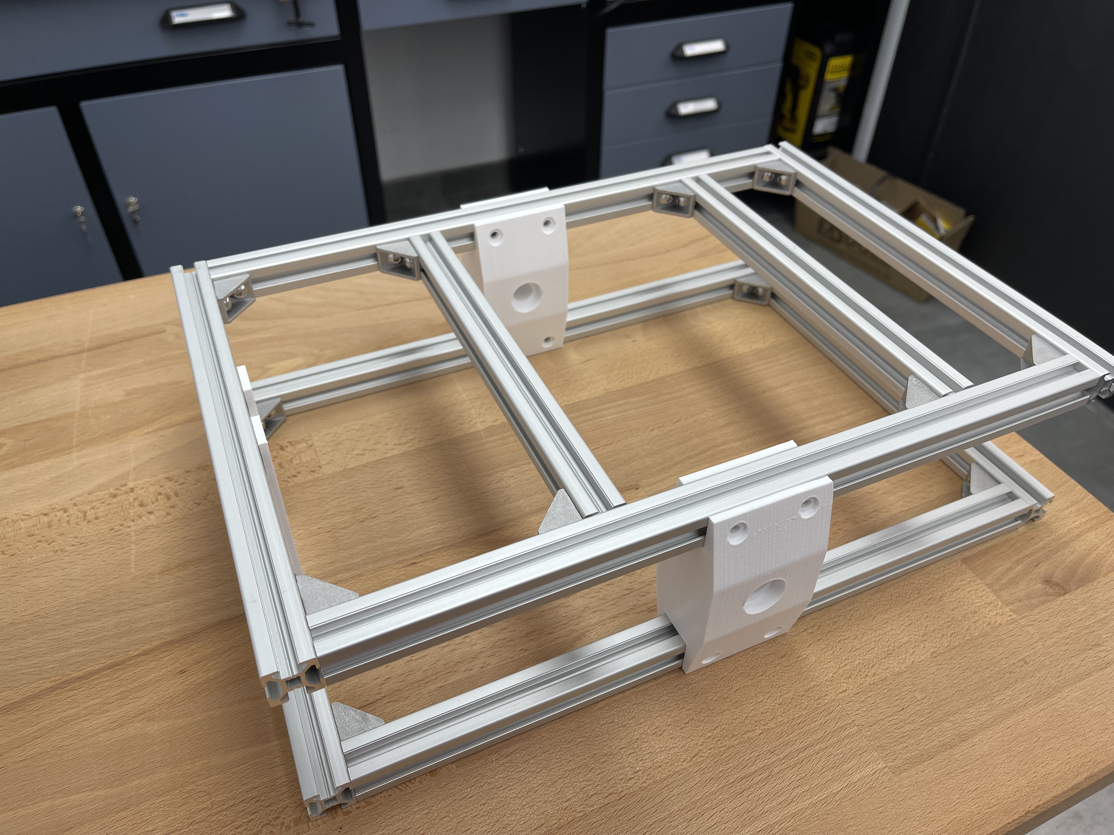
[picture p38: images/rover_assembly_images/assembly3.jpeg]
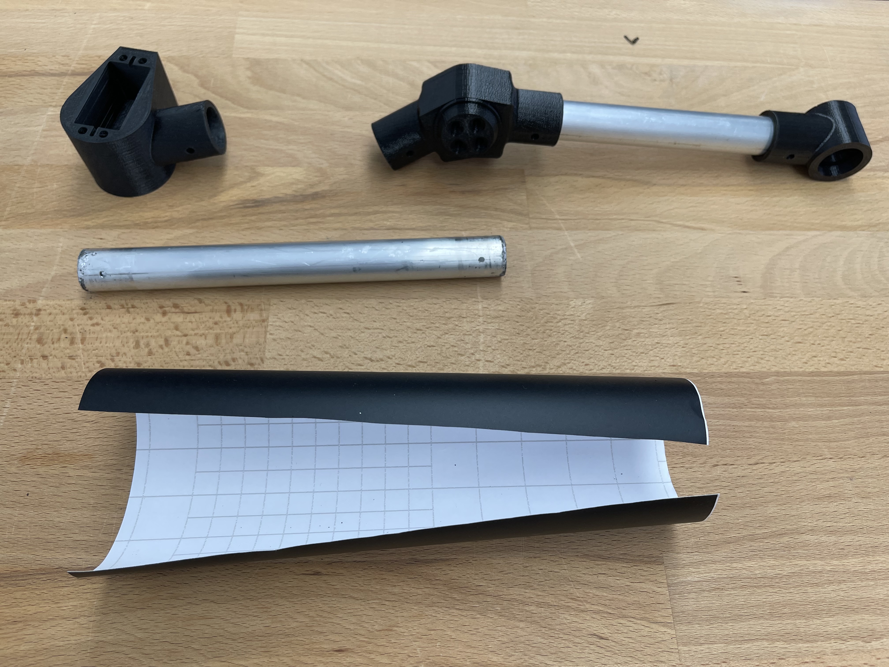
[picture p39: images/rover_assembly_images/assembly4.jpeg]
|  |  |
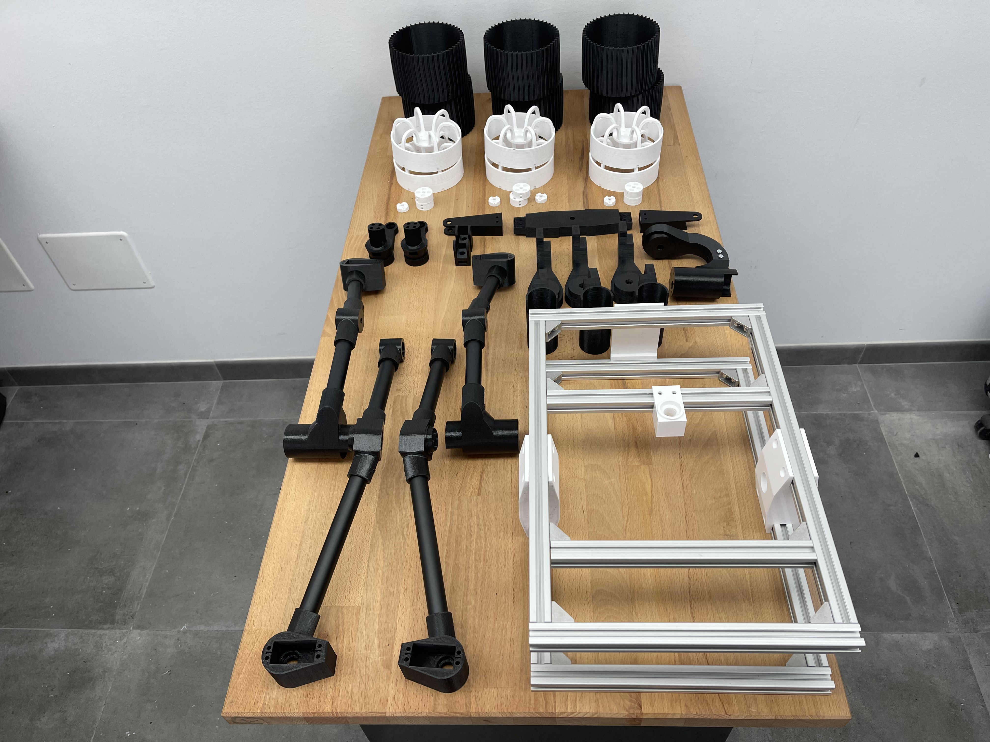
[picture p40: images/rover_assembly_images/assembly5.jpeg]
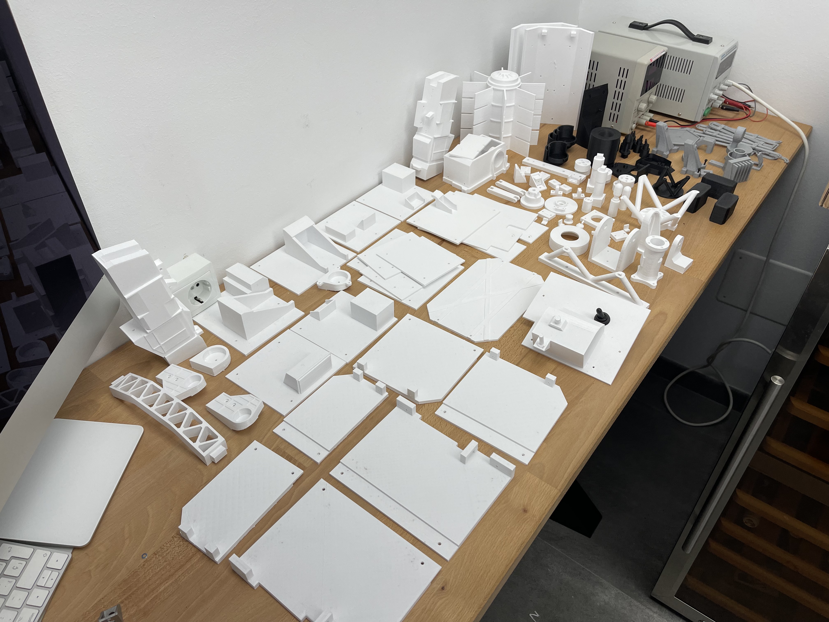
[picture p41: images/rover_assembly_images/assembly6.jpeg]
|  |  |
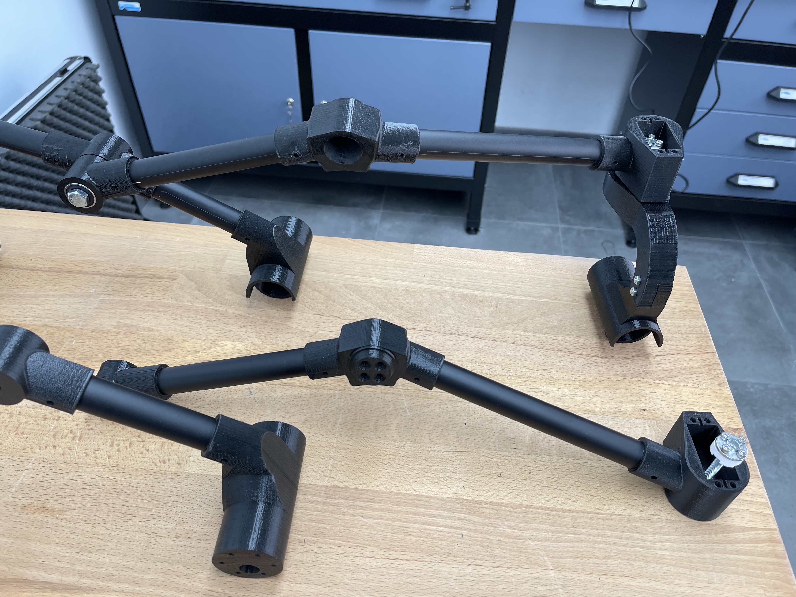
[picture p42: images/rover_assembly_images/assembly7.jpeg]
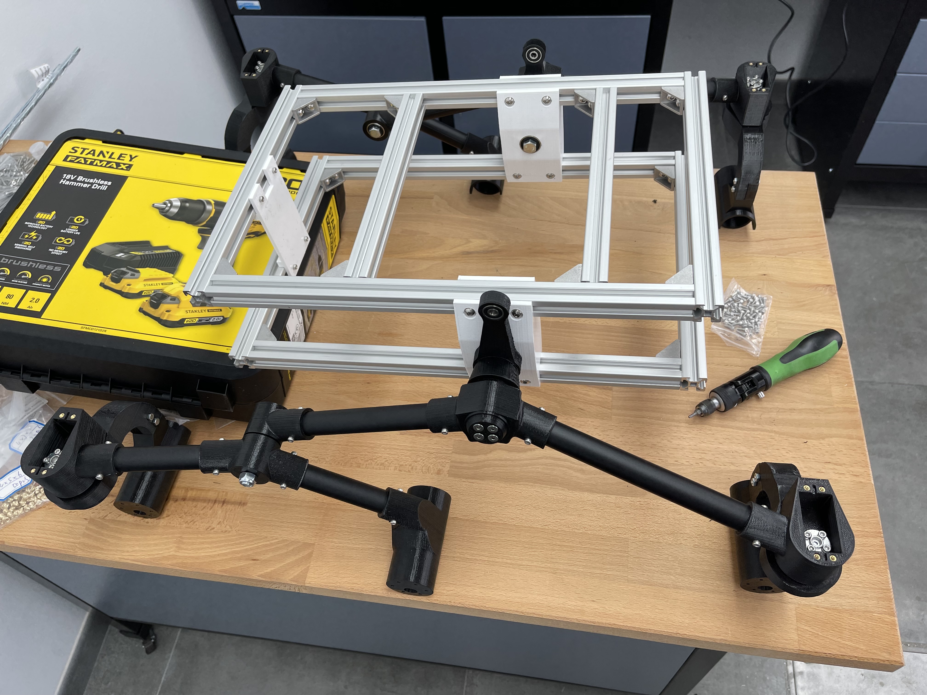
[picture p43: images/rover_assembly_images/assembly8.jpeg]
|  |  |
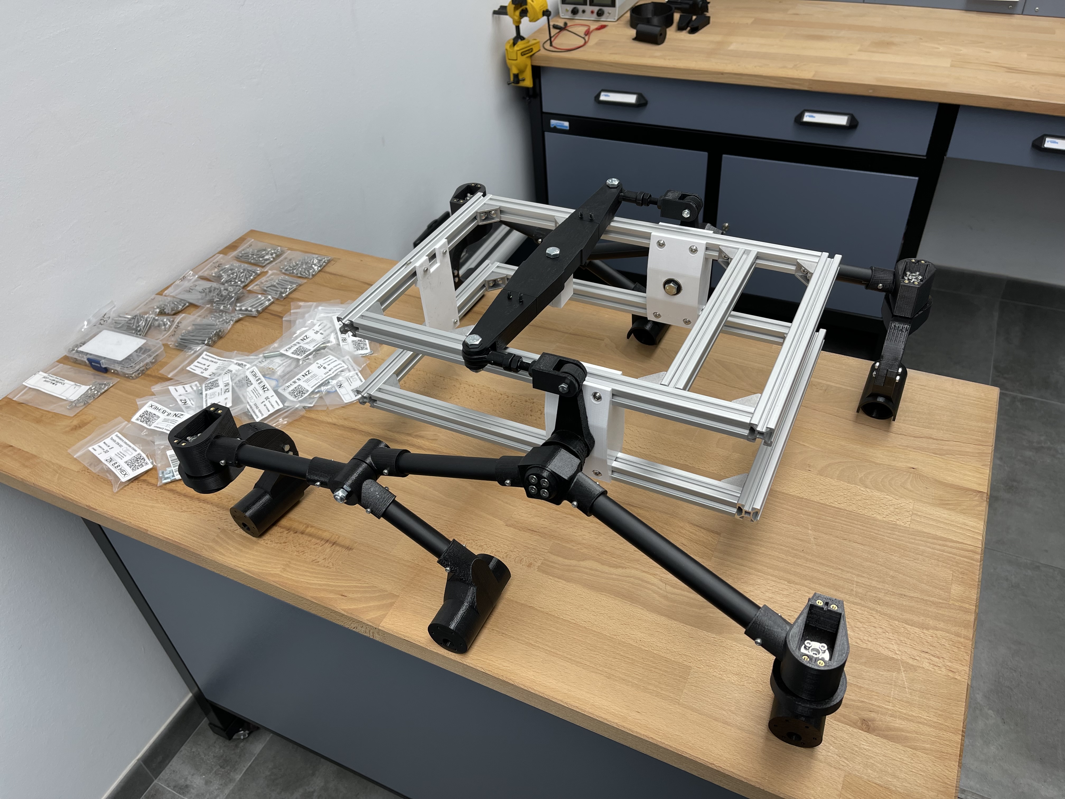
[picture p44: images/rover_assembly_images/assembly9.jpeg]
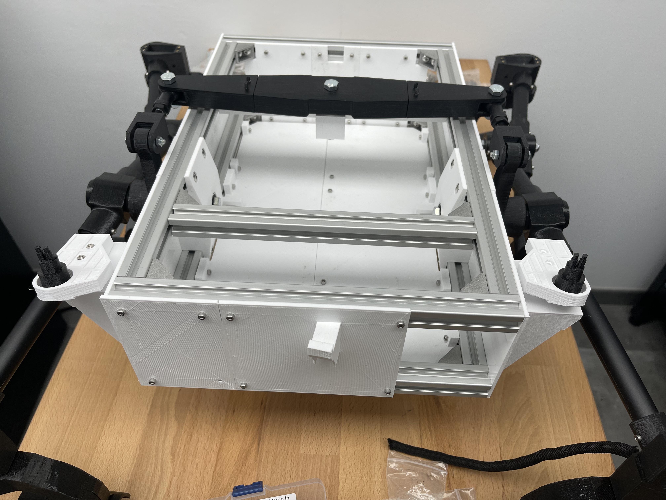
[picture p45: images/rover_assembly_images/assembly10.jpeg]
|  |  |
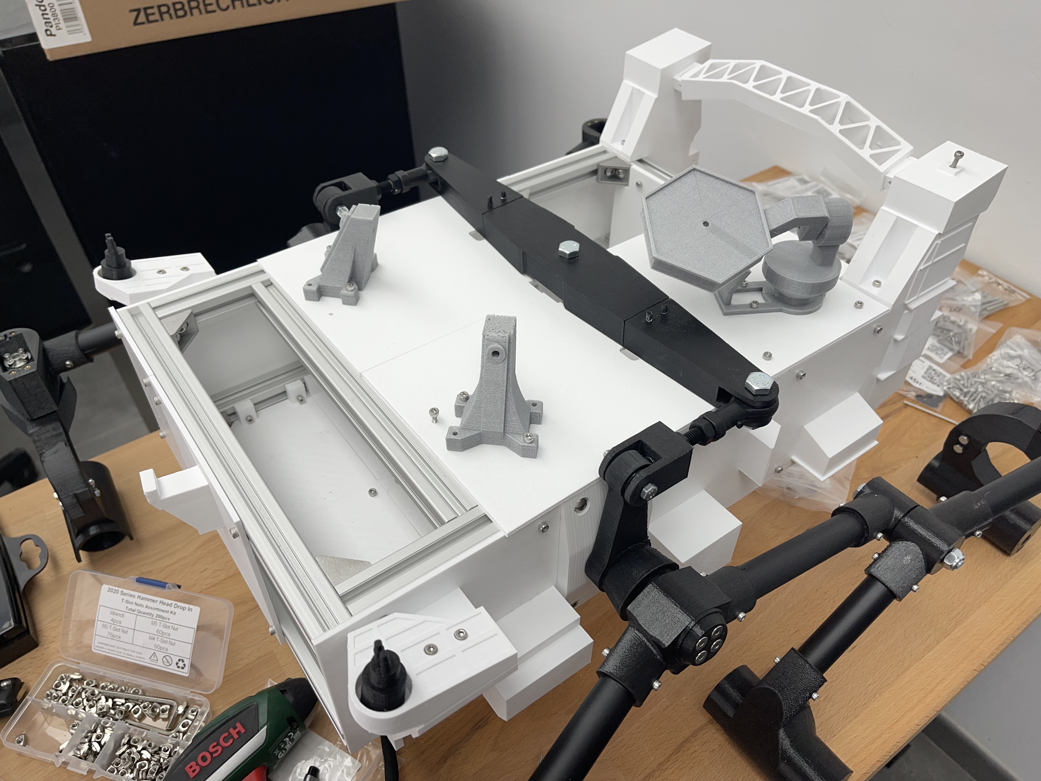
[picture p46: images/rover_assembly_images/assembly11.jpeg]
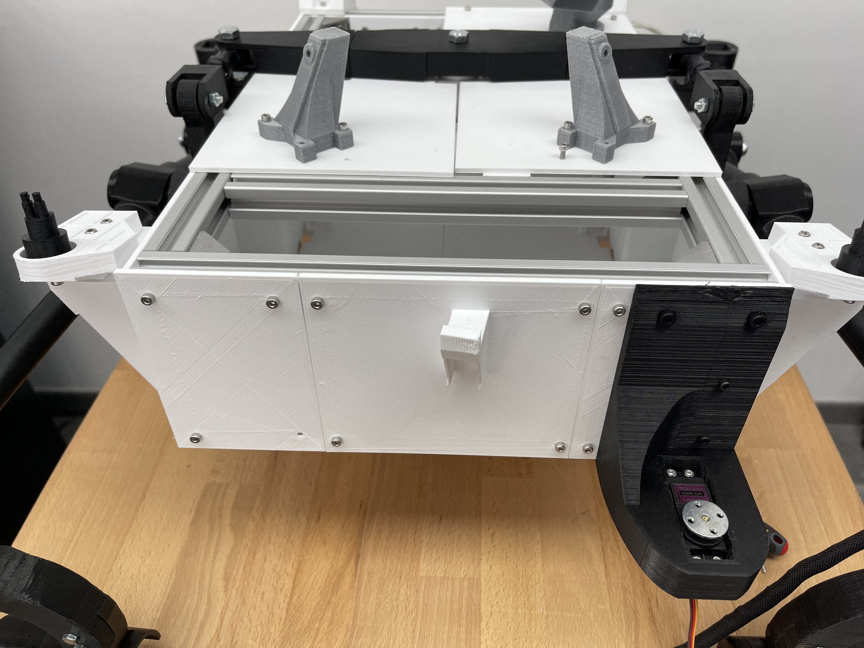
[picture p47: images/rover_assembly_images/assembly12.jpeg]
|  |  |
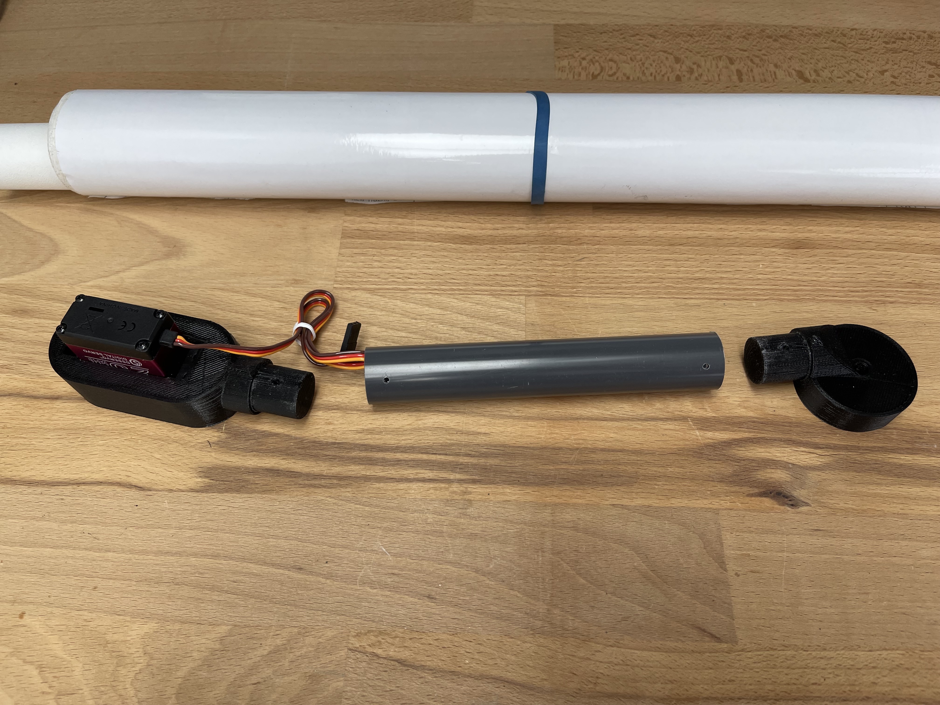
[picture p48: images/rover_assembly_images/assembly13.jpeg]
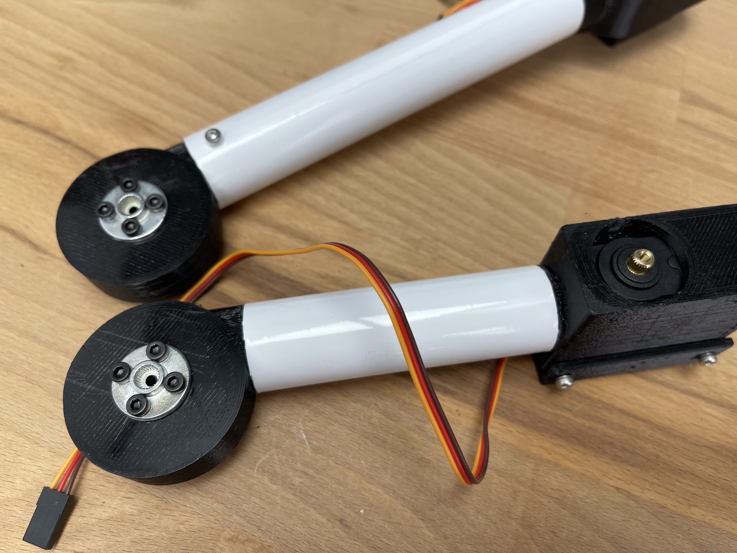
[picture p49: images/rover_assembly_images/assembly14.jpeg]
|  |  |
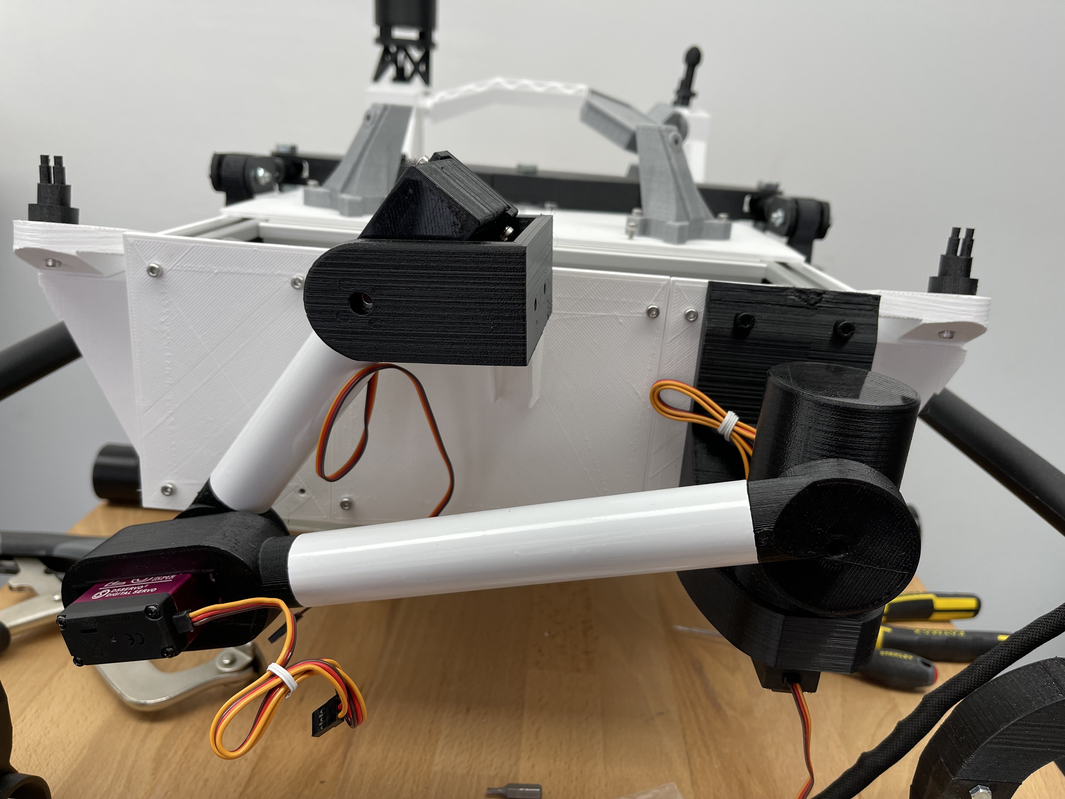
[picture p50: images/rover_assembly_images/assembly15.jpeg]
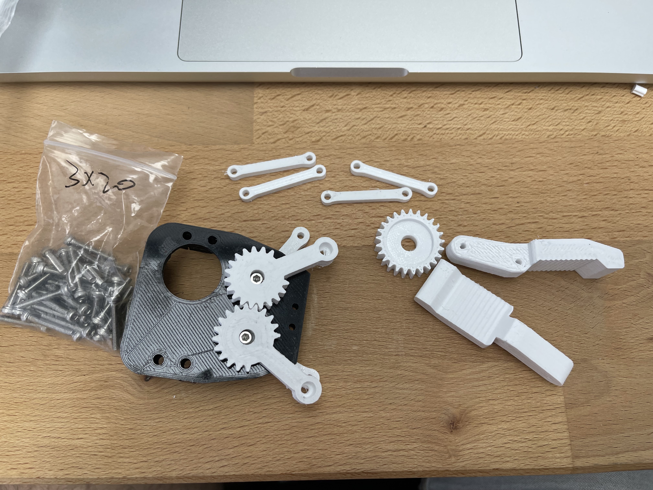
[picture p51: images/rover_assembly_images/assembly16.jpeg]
|  |  |
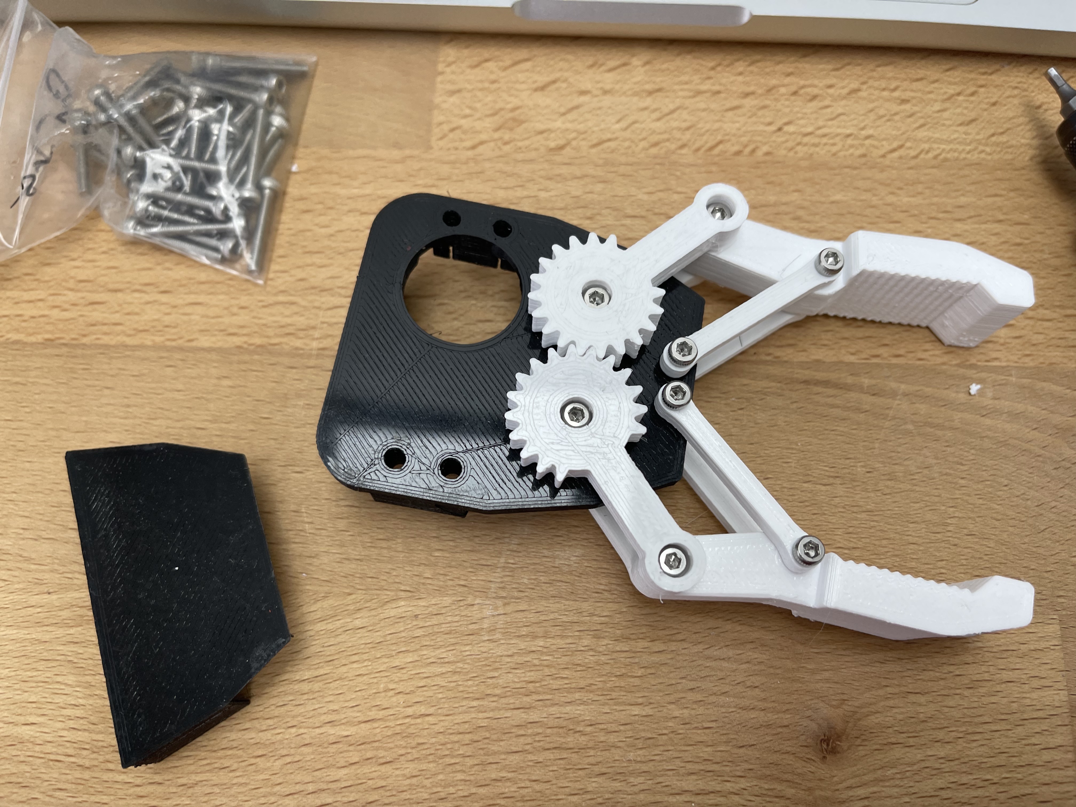
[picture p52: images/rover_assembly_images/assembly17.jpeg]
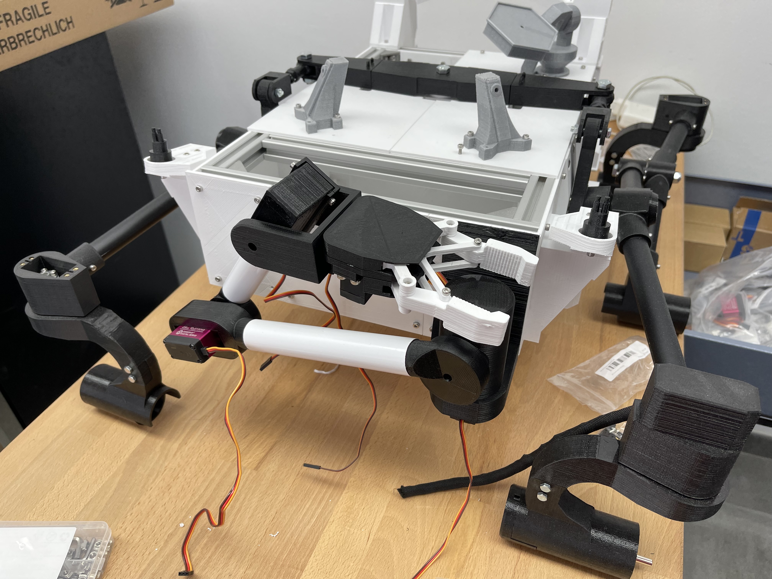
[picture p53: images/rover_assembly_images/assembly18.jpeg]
|  |  |
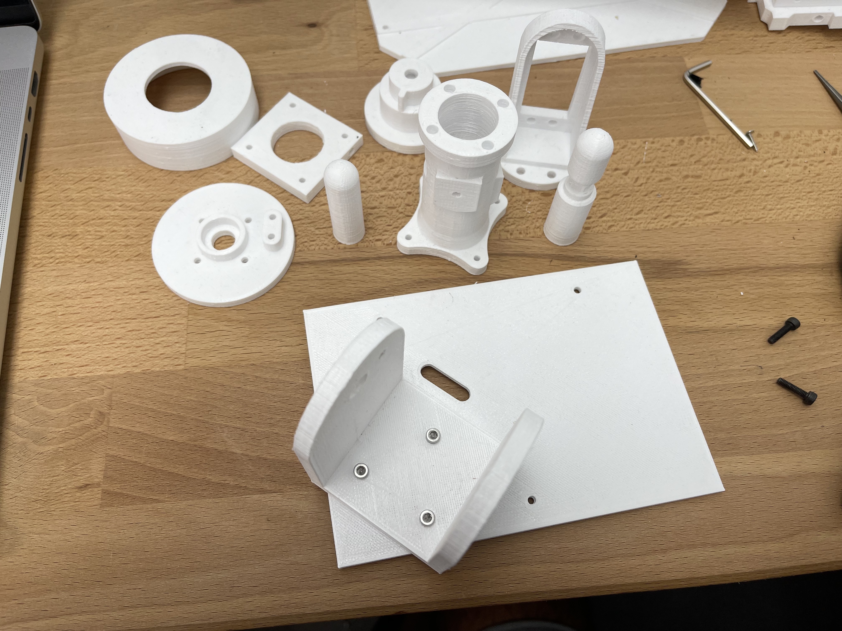
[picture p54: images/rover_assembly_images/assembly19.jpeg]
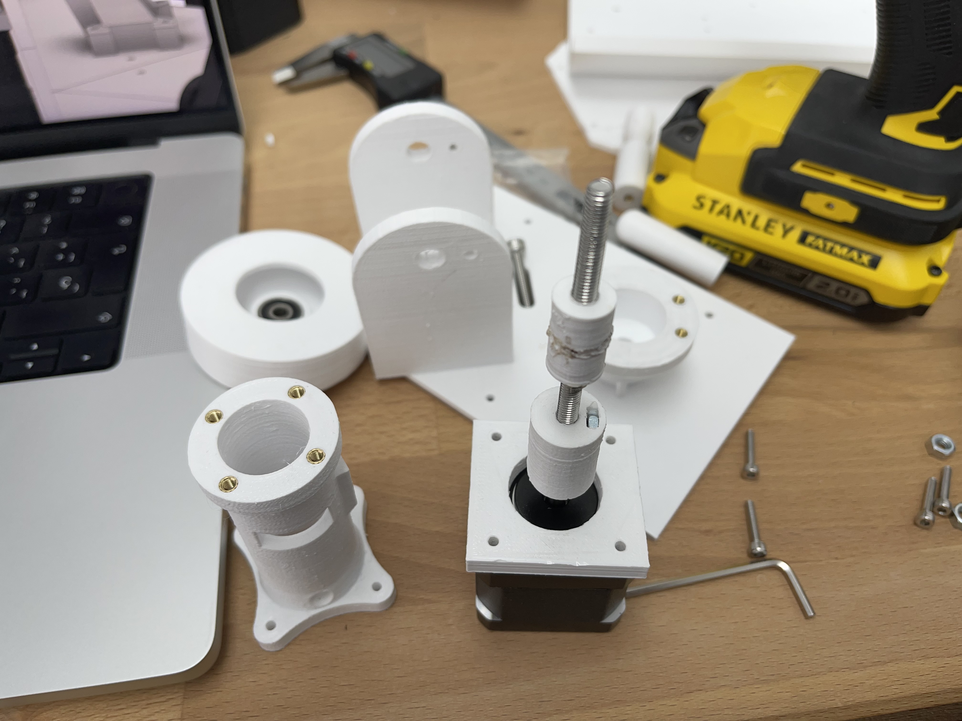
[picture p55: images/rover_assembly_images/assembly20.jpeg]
|  |  |
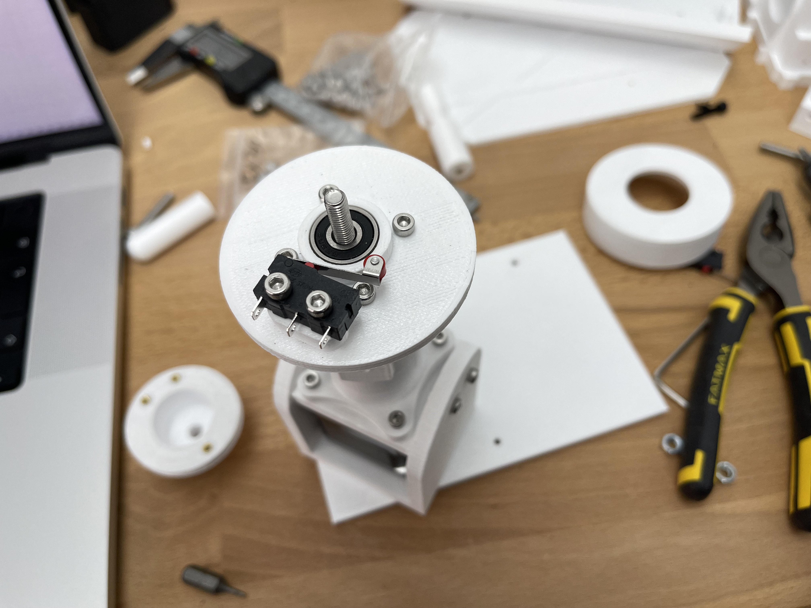
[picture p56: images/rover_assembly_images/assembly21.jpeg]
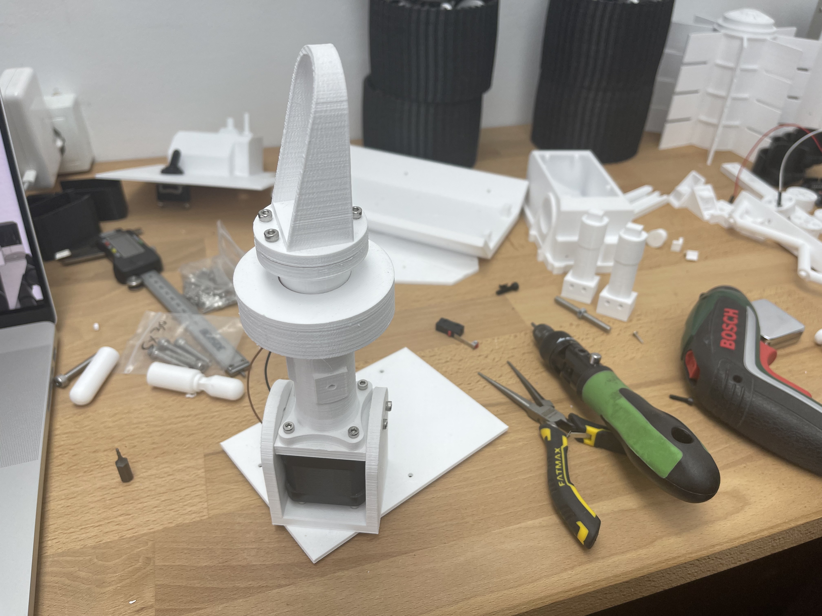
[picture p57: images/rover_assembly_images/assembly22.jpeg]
|  |  |
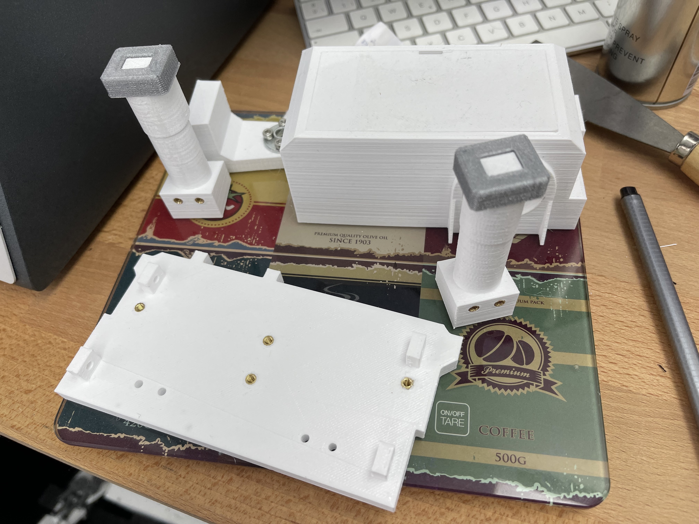
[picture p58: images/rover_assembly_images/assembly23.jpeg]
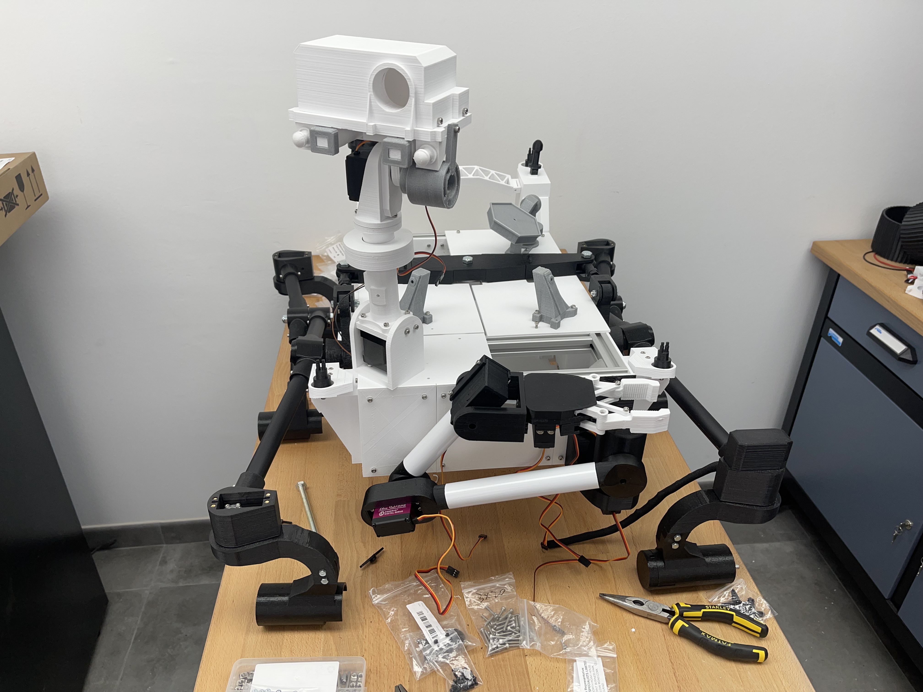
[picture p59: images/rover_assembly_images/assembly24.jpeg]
|  |  |
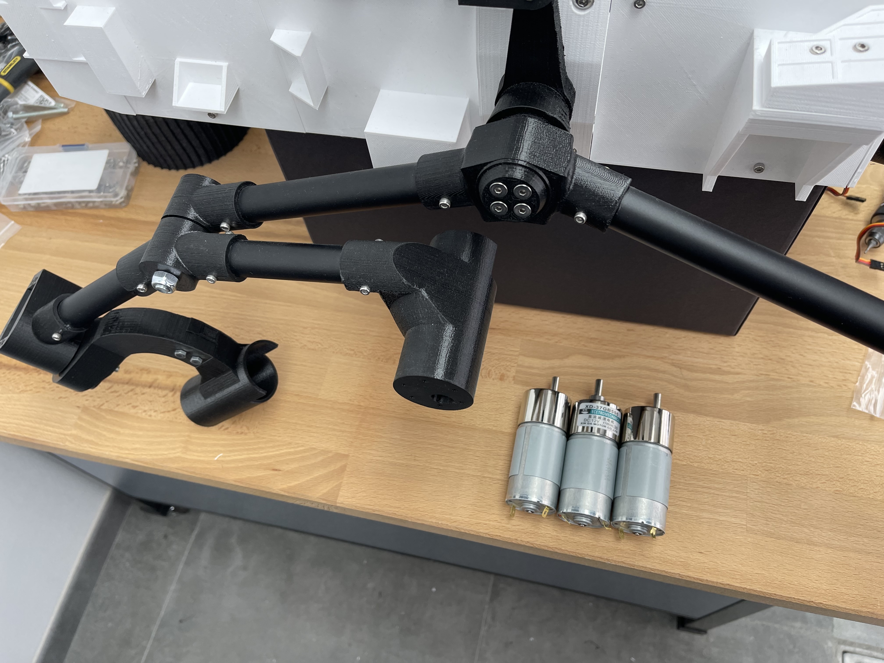
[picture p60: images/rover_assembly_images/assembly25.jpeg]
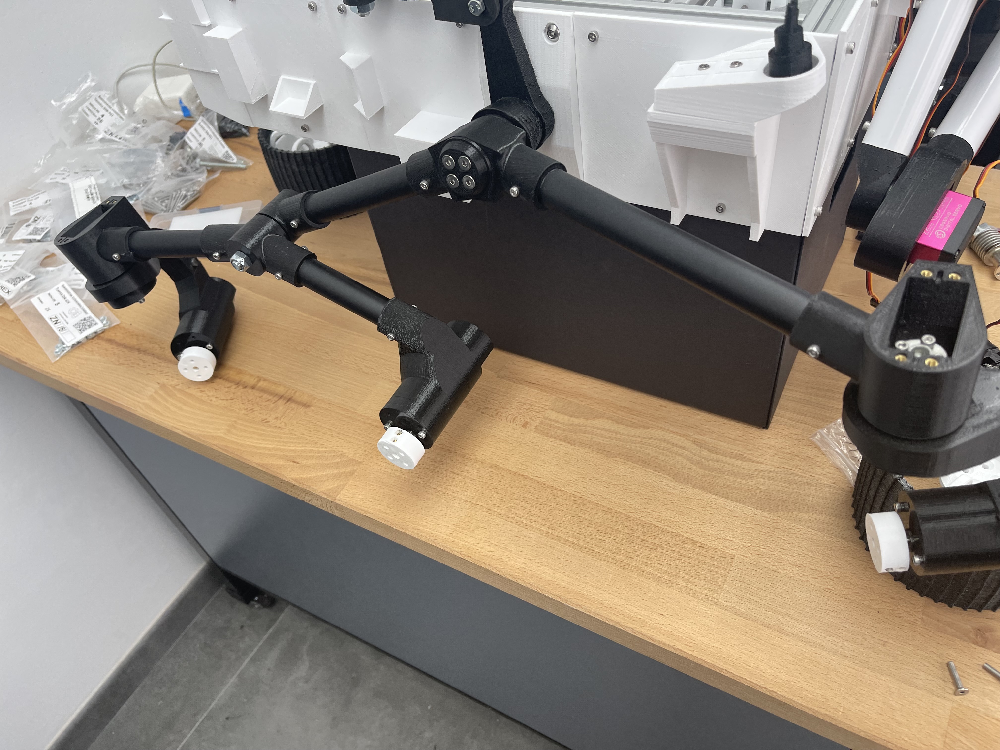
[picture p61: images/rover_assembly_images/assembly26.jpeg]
|  |  |
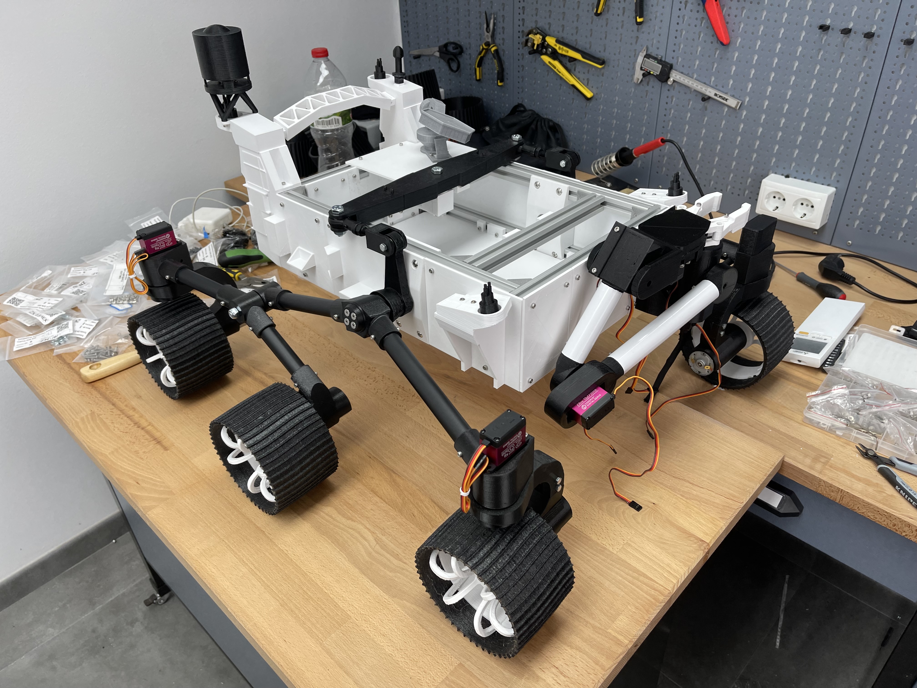
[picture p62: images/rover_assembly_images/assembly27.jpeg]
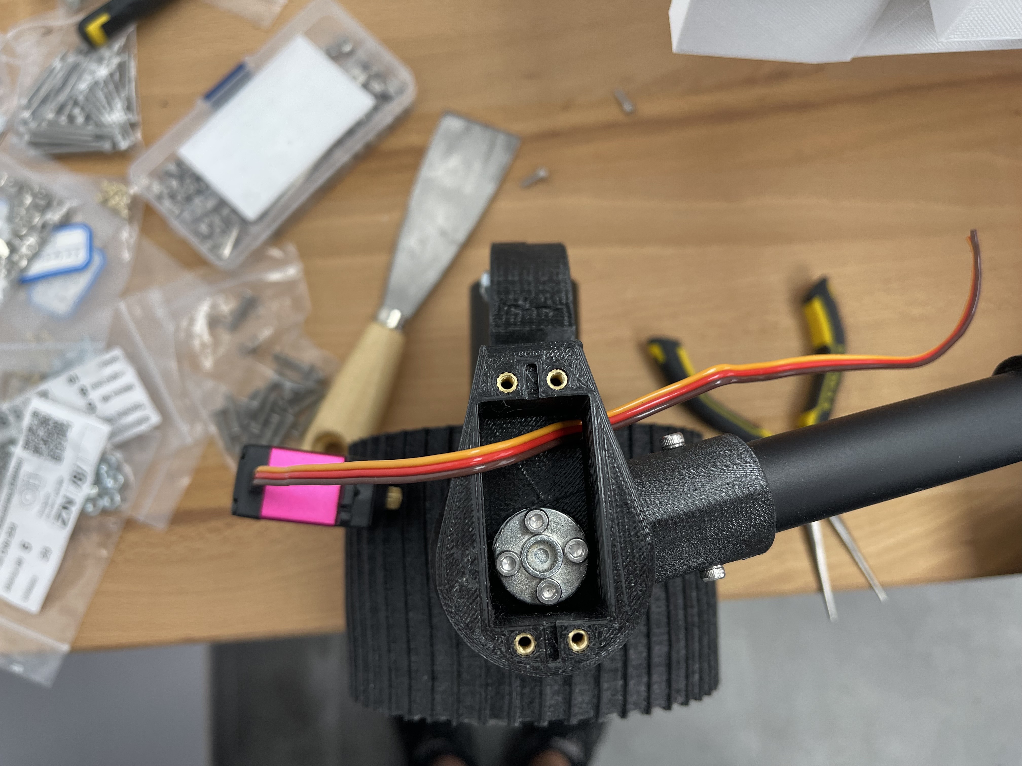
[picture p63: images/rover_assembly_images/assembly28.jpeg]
|  |  |
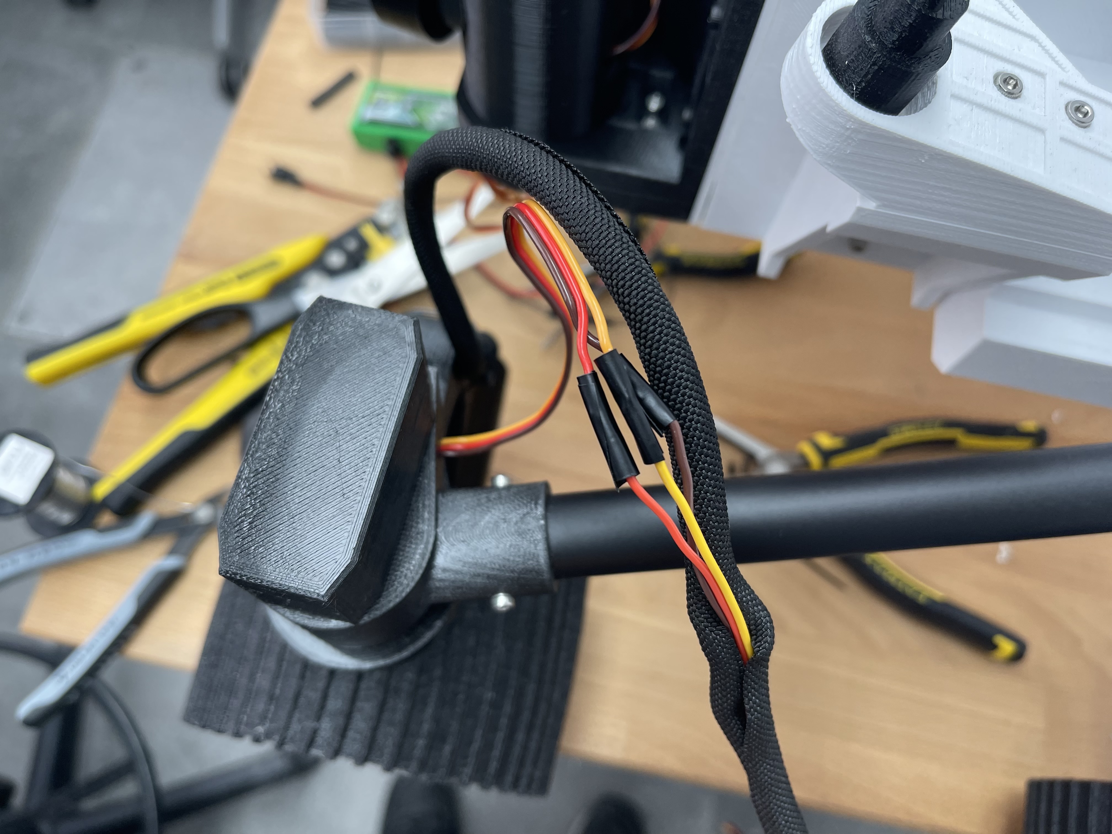
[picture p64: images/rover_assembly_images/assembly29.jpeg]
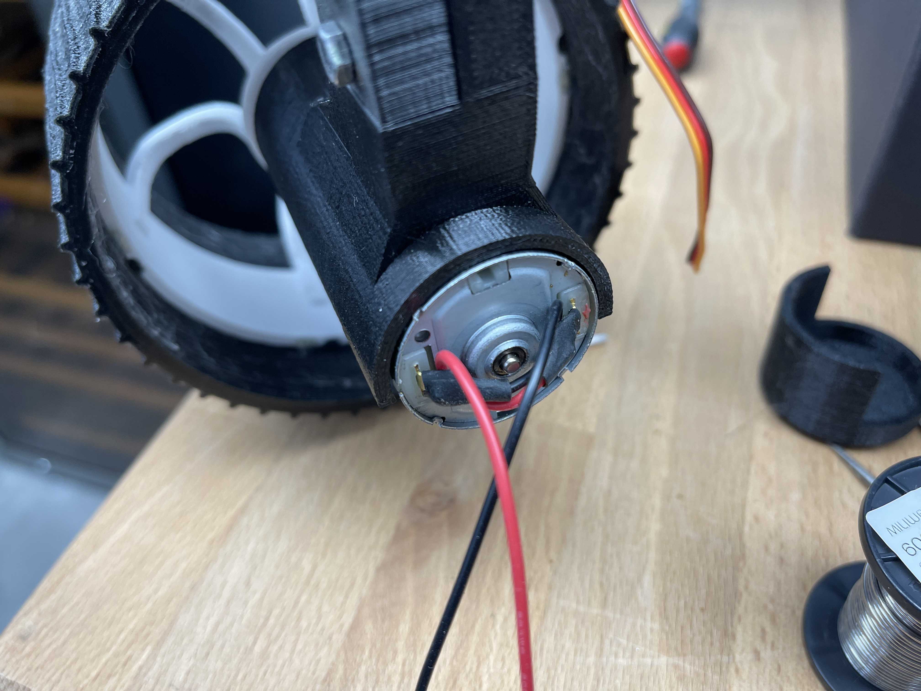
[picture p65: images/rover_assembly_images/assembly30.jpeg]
|  |  |
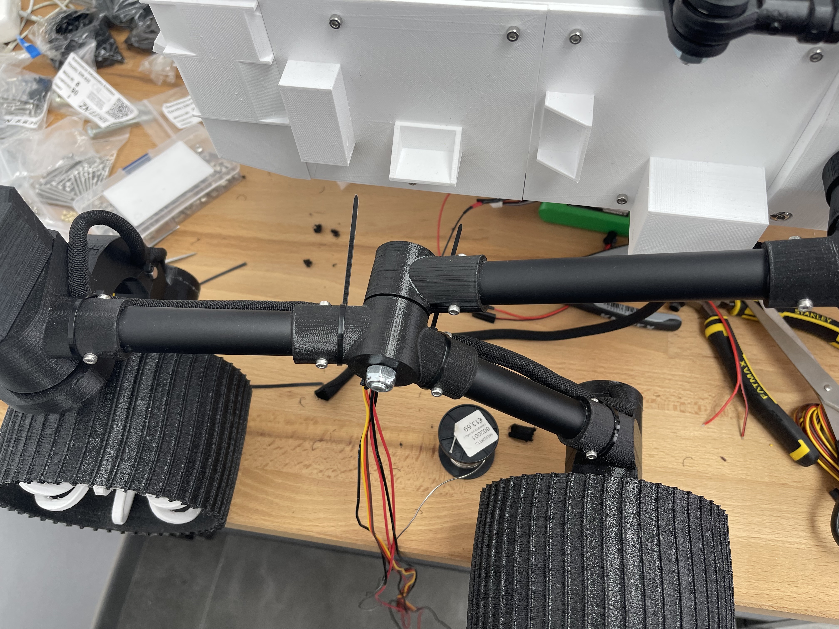
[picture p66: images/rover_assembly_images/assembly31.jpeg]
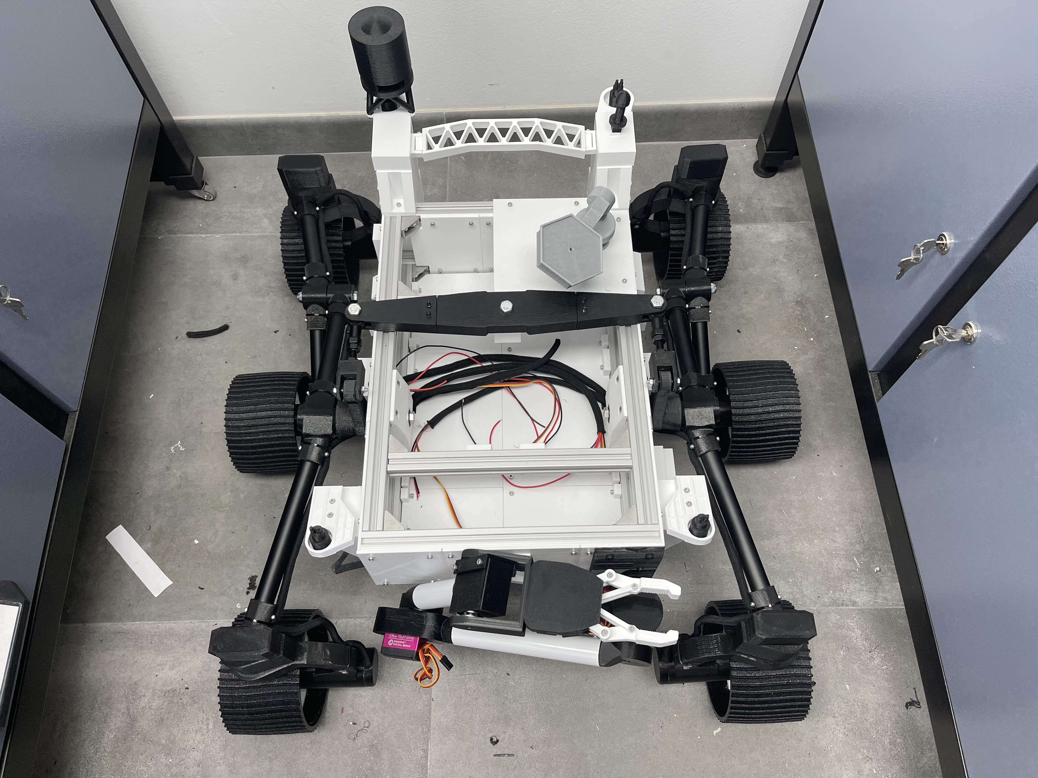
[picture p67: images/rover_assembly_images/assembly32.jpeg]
|  |  |
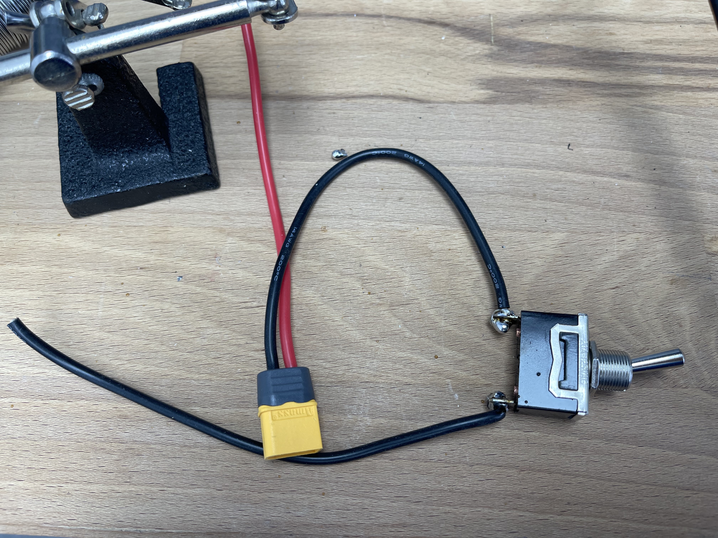
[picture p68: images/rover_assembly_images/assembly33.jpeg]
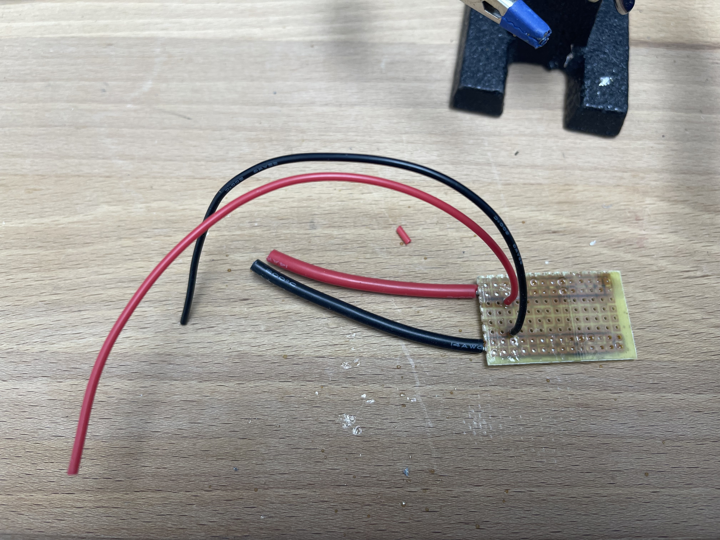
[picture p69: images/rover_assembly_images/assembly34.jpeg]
|  |  |
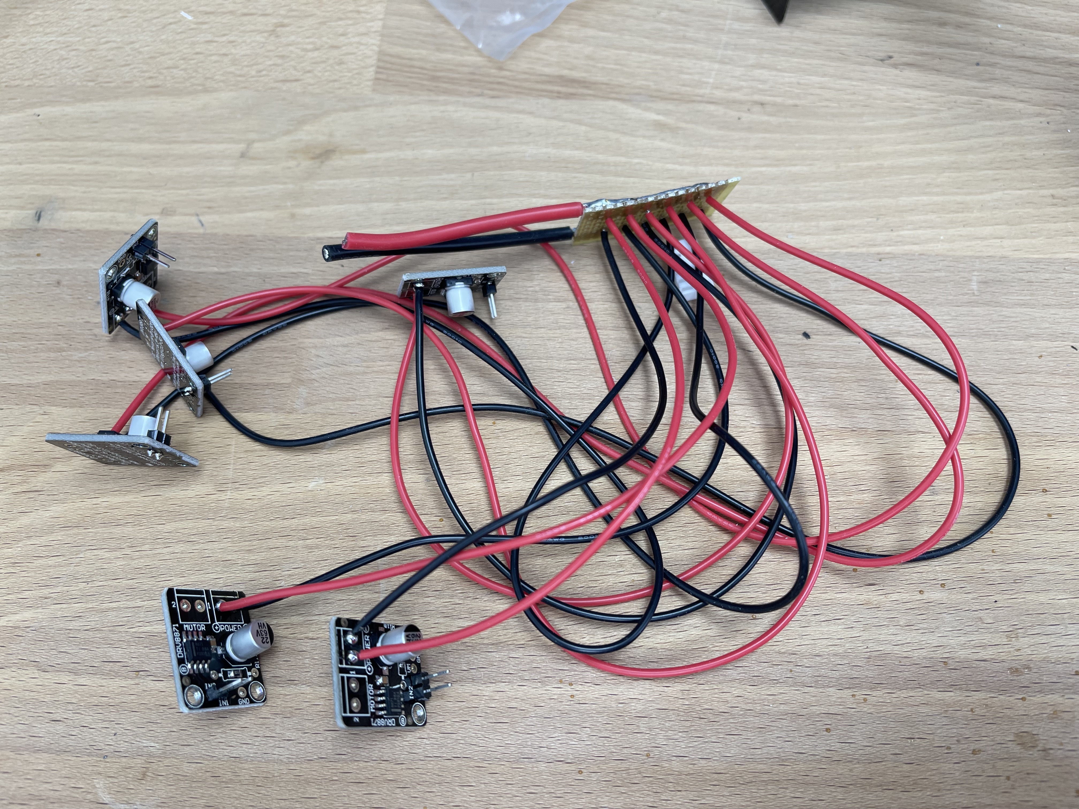
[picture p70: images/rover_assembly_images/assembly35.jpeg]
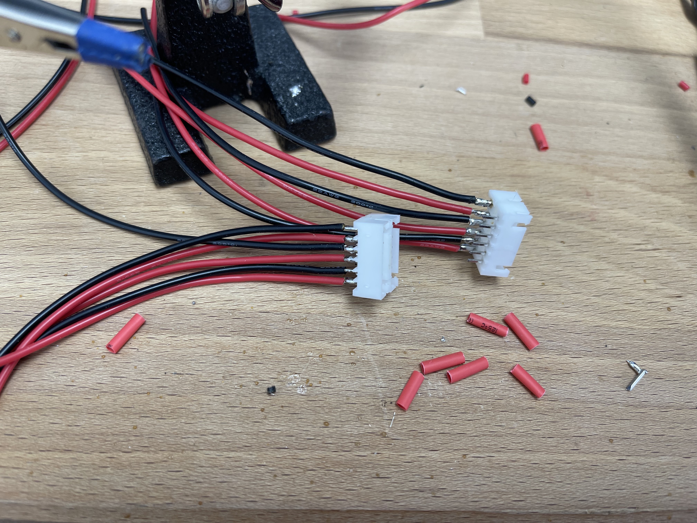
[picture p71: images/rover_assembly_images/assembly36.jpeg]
|  |  |
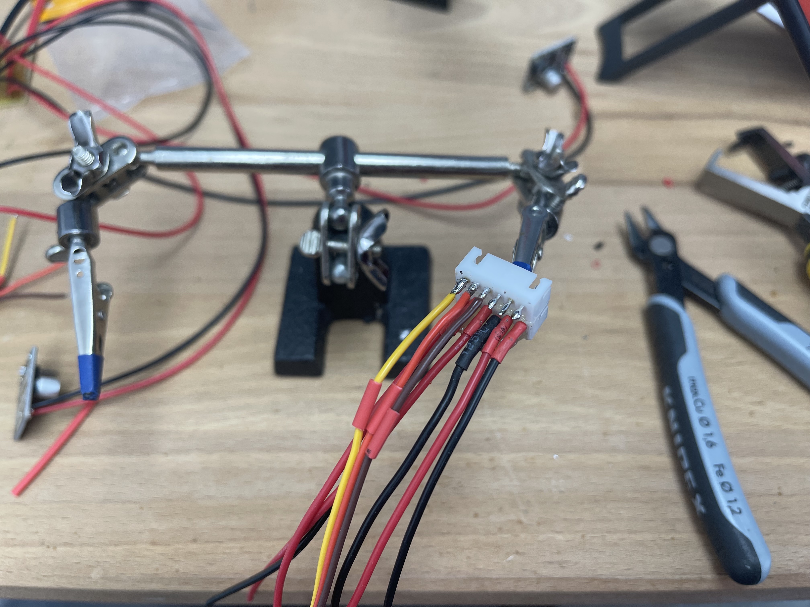
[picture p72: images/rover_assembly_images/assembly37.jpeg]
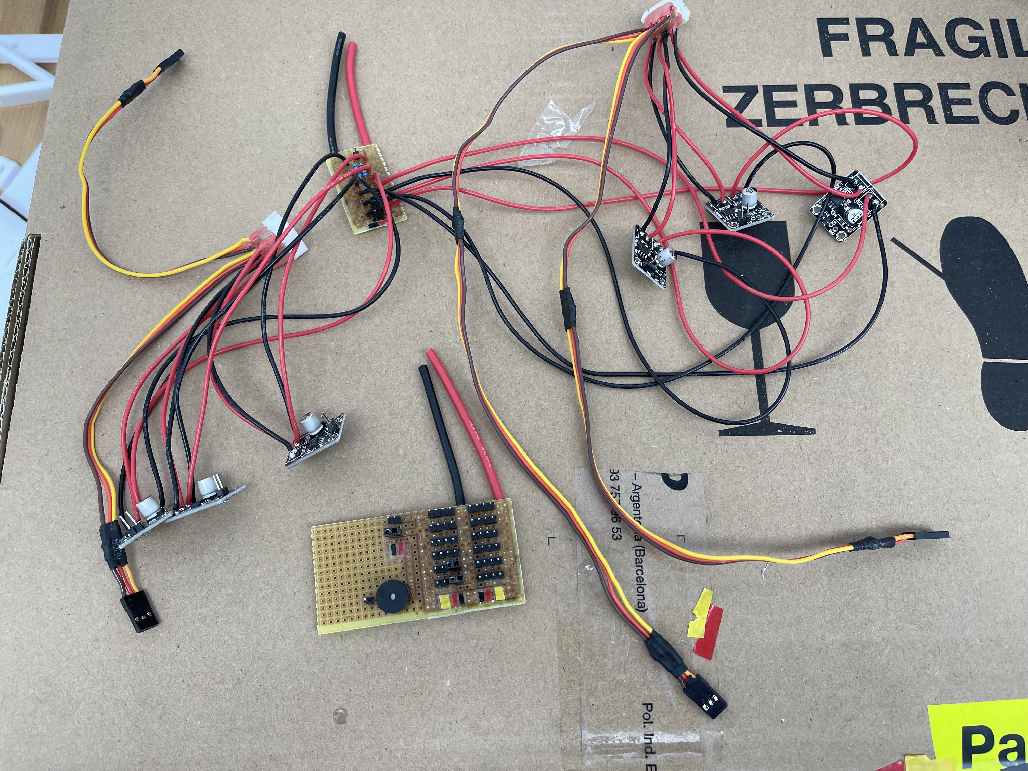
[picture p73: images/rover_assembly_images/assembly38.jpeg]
|  |  |
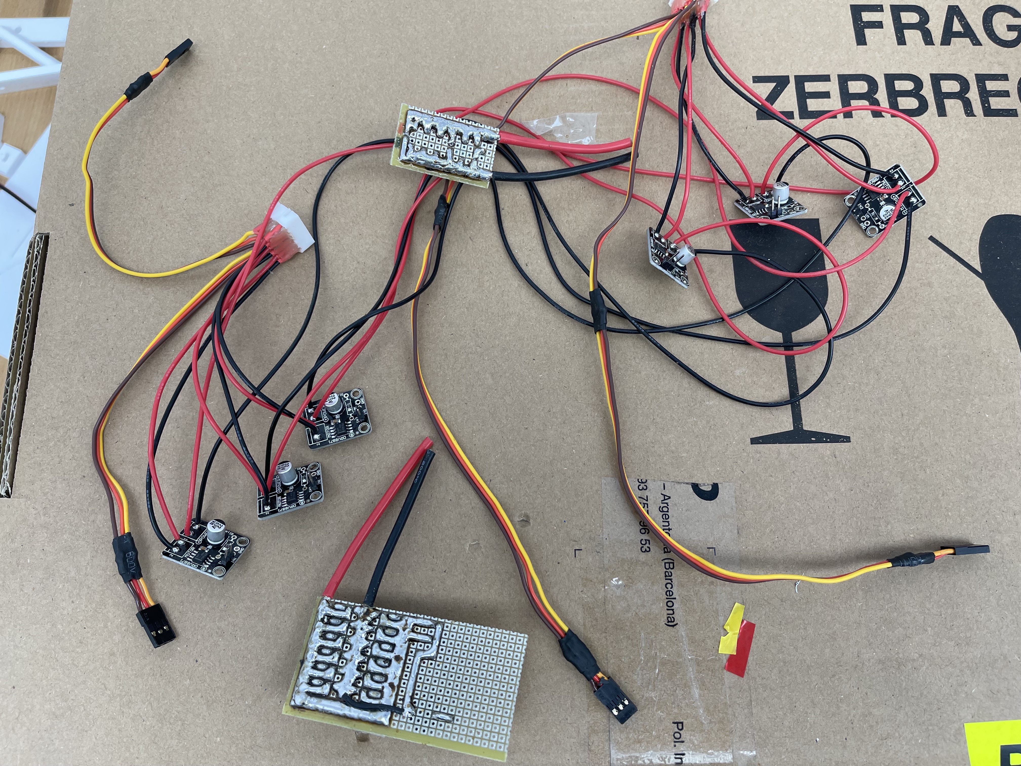
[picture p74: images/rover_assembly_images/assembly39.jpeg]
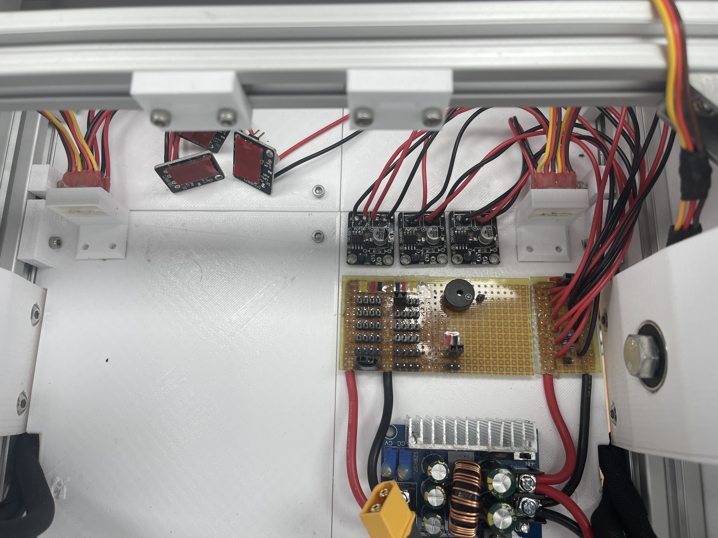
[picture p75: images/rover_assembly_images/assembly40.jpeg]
|  |  |
|  |  |
|  |  |
|  |  |
|  |  |
|  |  |
|  |  |
|  |  |
|  |  |

## Custom remote control PCB assembly process

|  |  |
| --- | --- |
|  |  |
|  |  |
|  |  |
|  |  |
|  |  |

## Attachment for generic/commercial remote control assembly process

|  |  |
| --- | --- |
|  |  |
|  |  |
|  |  |
|  |  |
|  |  |

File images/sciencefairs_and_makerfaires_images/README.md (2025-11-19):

# Science fairs and makerfaires
Since this project was completed, I have attended several science fairs in Spain, where I have presented the project with the main aim of showing people how current manufacturing and prototyping techniques (e.g. 3D printing) and common development boards (e.g. Arduino, ESP32) can enable us to create almost anything we can imagine.

## Makerfaire 2025 at Lleida (Barcelona)







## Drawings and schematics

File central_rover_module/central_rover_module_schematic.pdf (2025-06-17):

# MAIN SWITCH BUCK CONVERTER XL40¹5 OUT-

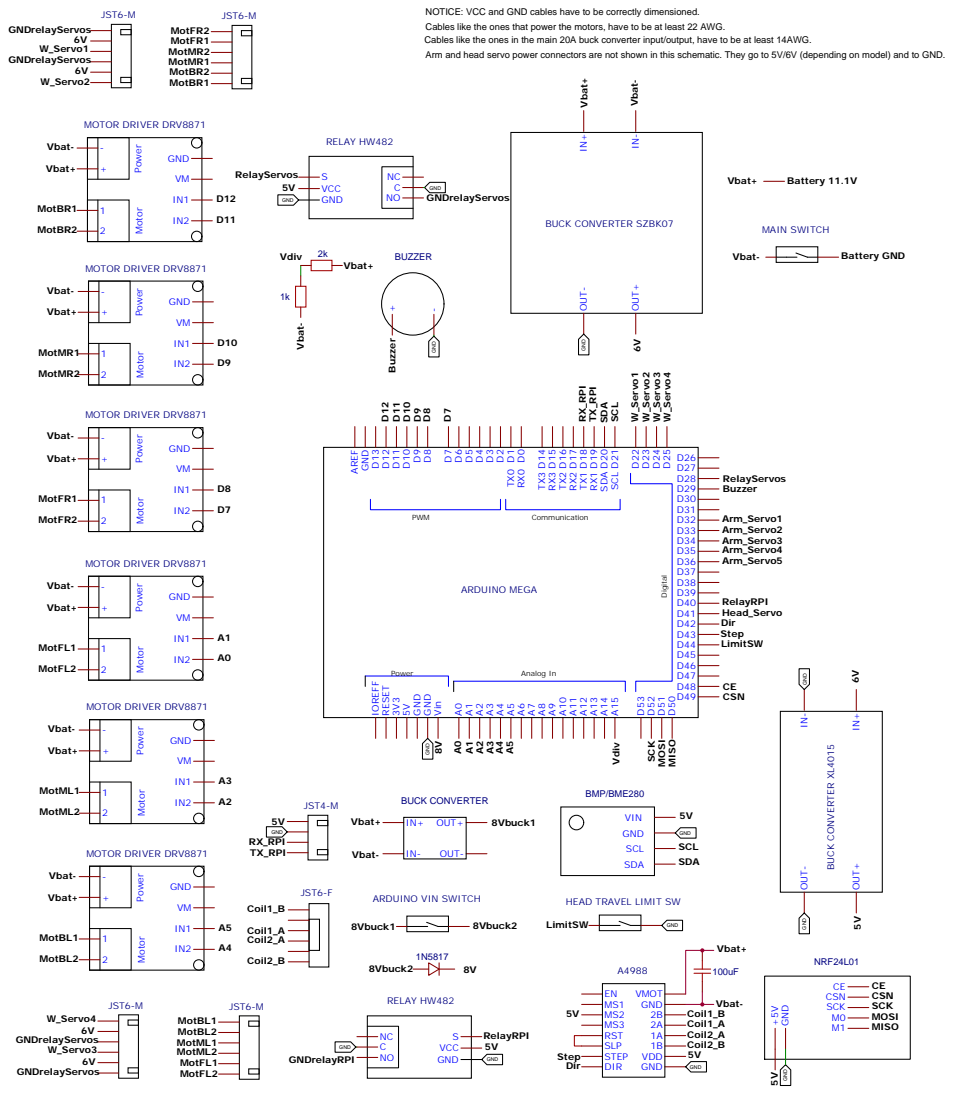
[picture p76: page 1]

NOTICE: VCC and GND cables have to be correctly dimensioned.
Cables like the ones that power the motors, have to be at least 22 AWG.
Arm and head servo power connectors are not shown in this schematic. They go to 5V/6V (depending on model) and to GND. RX_RPI TX_RPI

ARDUINO MEGA A¹A2A3A4A5A6A7A8A9A¹0 A¹¹ A¹2 A¹3 A¹4 A¹5 TX0 D¹ RX0 D0 TX3 D¹4 RX3 D¹5 TX2 D¹6 RX2 D¹⁷ TX¹ D¹8 RX¹ D¹9 SDA D20 SCL D2¹

HEAD TRAVEL LIMIT SW

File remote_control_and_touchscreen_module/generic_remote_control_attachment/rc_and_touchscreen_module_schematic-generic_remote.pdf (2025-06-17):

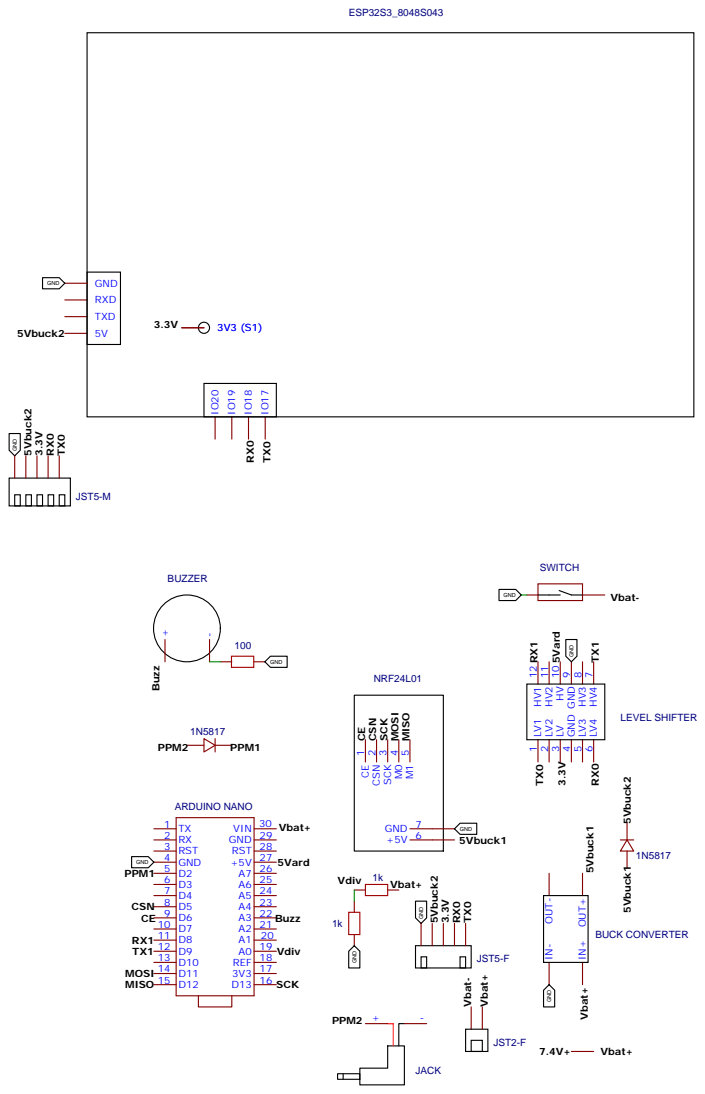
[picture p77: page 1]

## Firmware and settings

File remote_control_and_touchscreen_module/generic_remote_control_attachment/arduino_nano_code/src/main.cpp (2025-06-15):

#include <Arduino.h>
#include <RcTrainer.h>
#include <AltSoftSerial.h>

#include "SerialTransfer.h"
#include <Wire.h>

#include <SPI.h>
#include <nRF24L01.h>
#include <RF24.h>

#include "frameTypesDefinition.h"


// By default we listen on interrupt 0, which in Arduino nano, is digital input pin D2
RcTrainer tx;

RF24 radio(6, 5); // CE, CSN
const byte readAddress[6] = "ADDR2";
const byte writeAddress[6] = "ADDR1";

typedef struct {
  int y1;
  int x1;
  int y2;
  int x2;
  int aux1;
  int aux2;
  int aux3;
  int aux4;
  bool dataValid;
} RcValues;

typedef struct {
  float cellVoltage;
  int percentage;
  bool dataValid;
} BatteryValues;

typedef struct __attribute__((packed)) {
  uint8_t type; //Integer value identifying the type of frame
  int16_t data2B[4]; //Large data to be sent (2 bytes each) (ex.- joystick values -255...255)
  uint8_t data1B[5]; //Small data to be sent (1 byte each)
  //TODO: Add field for checksum/validation?
} Frame; //The same struct is used for radio and serial


AltSoftSerial mySerial; //RX = 8, TX = 9
//auto &mySerial = Serial;
SerialTransfer myTransfer;

const int batt_input_pin = A0; //Analog pin where the battery voltage is read
const int buzzer_pin = A3; //Analog pin where the buzzer is connected

bool radioControlEnabled = false;


void setup() {

    Serial.begin(38400);  
    mySerial.begin(38400);
    myTransfer.begin(mySerial);

    radio.begin();
    radio.openReadingPipe(0, readAddress);
    radio.openWritingPipe(writeAddress);
    radio.setPALevel(RF24_PA_MAX);

    pinMode(batt_input_pin, INPUT);
    pinMode(buzzer_pin, OUTPUT);

    noTone(buzzer_pin);

}


void serialSendFrame(Frame frame) {

  if (frame.type != NOT_VALID) {
    myTransfer.sendDatum(frame);
  }

}

Frame rcValuesToFrame(RcValues rcValues) {

  Frame frame;

  frame.type = INF_F_RC_VALUES;
  frame.data2B[0] = rcValues.y1;
  frame.data2B[1] = rcValues.x1;
  frame.data2B[2] = rcValues.y2;
  frame.data2B[3] = rcValues.x2;
  frame.data1B[0] = rcValues.aux1;
  frame.data1B[1] = rcValues.aux2;
  frame.data1B[2] = rcValues.aux3;
  frame.data1B[3] = rcValues.aux4;

  return frame;

}

void serialSendRcValuesFrame(RcValues rcValues) {

  if (rcValues.dataValid) {
    
    Frame frame = rcValuesToFrame(rcValues);
    serialSendFrame(frame);

  }

}

Frame rcBattValuesToFrame(BatteryValues battValues) {

  Frame frame;
  
  frame.type = INF_F_RC_BAT_LEVEL;
  frame.data1B[0] = battValues.cellVoltage * 10; //We multiply by 10 because the float data is sent as an integer
  frame.data1B[1] = battValues.percentage;

  return frame;

}

void serialSendBattValuesFrame(BatteryValues battValues) {

  if (battValues.dataValid) {

    Frame frame = rcBattValuesToFrame(battValues);

    serialSendFrame(frame);

  }

}

Frame serialReceiveFrame() {

  Frame frame;
  frame.type = NOT_VALID;

  if (myTransfer.available()) {

    myTransfer.rxObj(frame);

    return frame;

  }

  return frame;
  
}

Frame radioReceiveFrame() {

  Frame frame;
  frame.type = NOT_VALID;

  radio.startListening();

  if(radio.available()) {

    radio.read(&frame, sizeof(frame));

    return frame;

  }

  return frame;

}

void radioSendFrame(Frame frame) {

  if (frame.type != NOT_VALID) {
    radio.stopListening();
    radio.write(&frame, sizeof(frame));
  }
  
}

void radioSendRcValuesFrame(RcValues rcValues) {

  if (rcValues.dataValid) {
    
    Frame frame = rcValuesToFrame(rcValues);
    radioSendFrame(frame);

  }

}


BatteryValues getBatteryValues() {

  //We are using a Lithium-Ion battery for the RC remote
  //We get the battery level every second

  static unsigned long previousMillis = 0;
  BatteryValues battValues;

  battValues.dataValid = false;

  if (millis() - previousMillis >= 1000) { 

    previousMillis = millis();

    int batt_divider_voltage_analog_value;  //Analog value read from the voltage divider output, which is approximately 4V when the battery is fully charged
    float batt_divider_voltage; //Volts of the voltage divider output. The voltage divider in the radio controller halves the voltage of the battery.
    int batt_percentage; //Percentage of the battery, from 0% (3.3V per cell) to 100% (4.2V per cell)

    batt_divider_voltage_analog_value = analogRead(batt_input_pin);

    batt_divider_voltage = (5.00 / 1023) * batt_divider_voltage_analog_value;

    //Notice: The max charge of the battery will be 4.2V per cell, 8.4V in total (2S battery).

    batt_percentage = map(batt_divider_voltage * 100, 4.2 * 100, 3.3 * 100, 100, 0); //We multiply by 100 because the map() function does not accept floats.

    if (batt_divider_voltage <= 3.3) {
      batt_percentage = 0;
    }

    battValues.cellVoltage = batt_divider_voltage;
    battValues.percentage = batt_percentage;
    battValues.dataValid = true;

  }

  return battValues;

}

//TODO: This is a test function. Delete on final or near-final version. 
void makeBuzzerSound() {

  static unsigned long previousMillis = 0;

  if (millis() - previousMillis >=10000) {
    previousMillis = millis();
    tone(buzzer_pin, 1000, 100);
  }

}

//We need to correct the values of the RC remote, because the values are not centered at 0, and we want a range of -255..255 in each axis
void correctRcValues(RcValues &rcValues) {

  if (rcValues.x1 > 470 && rcValues.x1 < 550) {
   rcValues.x1 = 0;
  } else {
    if (rcValues.x1 <= 470) {
      rcValues.x1 = map(rcValues.x1, 470, 0, -1, -255);
    } else {
      rcValues.x1 = map(rcValues.x1, 550, 1023, 0, 255);
    }
  }

  if (rcValues.y1 > 470 && rcValues.y1 < 550) {
   rcValues.y1 = 0;
  } else {
    if (rcValues.y1 <= 470) {
      rcValues.y1 = map(rcValues.y1, 470, 0, -1, -255);
    } else {
      rcValues.y1 = map(rcValues.y1, 550, 1023, 0, 255);
    }
  }

  if (rcValues.x2 > 470 && rcValues.x2 < 550) {
   rcValues.x2 = 0;
  } else {
    if (rcValues.x2 <= 470) {
      rcValues.x2 = map(rcValues.x2, 470, 0, -1, -255);
    } else {
      rcValues.x2 = map(rcValues.x2, 550, 1023, 0, 255);
    }
  }

  if (rcValues.y2 > 470 && rcValues.y2 < 550) {
   rcValues.y2 = 0;
  } else {
    if (rcValues.y2 <= 470) {
      rcValues.y2 = map(rcValues.y2, 470, 0, -1, -255);
    } else {
      rcValues.y2 = map(rcValues.y2, 550, 1023, 0, 255);
    }
  }

  //TODO: Once the final use of each AUX is determined, we will map the values to the correct range (ex.- 0..1)
  rcValues.aux1 = map(rcValues.aux1, 0, 1023, 0, 255); 
  rcValues.aux2 = map(rcValues.aux2, 0, 1023, 0, 255);
  rcValues.aux3 = map(rcValues.aux3, 0, 1023, 0, 255);
  rcValues.aux4 = map(rcValues.aux4, 0, 1023, 0, 255); 

  if (rcValues.aux1 < 10) {
    rcValues.aux1 = 0;
  } else {
    rcValues.aux1 = 1;
  }

  if (rcValues.aux2 < 10) {
    rcValues.aux2 = 0;
  } else if (rcValues.aux2 > 245) {
    rcValues.aux2 = 2;
  } else {
    rcValues.aux2 = 1;
  }

  if (rcValues.aux3 < 10) {
    rcValues.aux3 = 0;
  } else {
    rcValues.aux3 = 1;
  }

  if (rcValues.aux4 < 10) {
    rcValues.aux4 = 0;
  } else if(rcValues.aux4 > 245) {
    rcValues.aux4 = 2;
  } else {
    rcValues.aux4 = 1;
  }
  
}

RcValues getSpektrumRcValues() {
  
  RcValues rcValues;

  rcValues.y1 = tx.getChannel(0);
  rcValues.x1 = tx.getChannel(3);
  rcValues.y2 = tx.getChannel(2);
  rcValues.x2 = tx.getChannel(1);
  rcValues.aux1 = tx.getChannel(4);
  rcValues.aux2 = tx.getChannel(5);
  rcValues.aux3 = tx.getChannel(6);
  rcValues.aux4 = tx.getChannel(7);

  rcValues.dataValid = true;

  correctRcValues(rcValues);

  return rcValues;

}

RcValues getSpektrumRcValuesForSerial () {
  
  RcValues rcValues;
  rcValues.dataValid = false;

  static unsigned long previousMillis = 0;

  //Gets the RC values every 130ms
  if (millis() - previousMillis >= 130) {
    previousMillis = millis();

    rcValues = getSpektrumRcValues();

  }

  return rcValues;

}

RcValues getSpektrumRcValuesForRadio () {
  
  RcValues rcValues;
  rcValues.dataValid = false;

  static unsigned long previousMillis = 0;

  //Gets the RC values every 50ms
  if (millis() - previousMillis >= 50) {
    previousMillis = millis();

    rcValues = getSpektrumRcValues();
    rcValues.dataValid = radioControlEnabled;

  }

  return rcValues;

}

bool rcRadioEnableStatusFromFrame(Frame frame) {
  return frame.data1B[0] == 1;
}

void handleReceivedFrame(Frame frame) {

  //Handles specific frames that must be handled by arduino nano, such as command frames 
  //to make buzzer sounds when the battery of the rc remote is low, or play a melody. 

  switch (frame.type) {

    case CMD_F_RC_BUZZER:
      tone(buzzer_pin, 1000, 100);
      break;

    case CMD_F_RC_RADIO_ENABLING:
      radioControlEnabled = rcRadioEnableStatusFromFrame(frame);
      break;

    case CMD_F_TEST:
      //TODO: Delete. Just for testing
      tone(buzzer_pin, 500, 100);

      Frame responseFrame;
      responseFrame.type = CMD_F_TEST;
      responseFrame.data2B[1] = frame.data2B[1];
      responseFrame.data1B[3] = frame.data1B[3];

      serialSendFrame(responseFrame);
      //
      break;

    default:
      break;

  }

}

void loop() {

    RcValues rcValues; 
    rcValues = getSpektrumRcValuesForSerial();
    serialSendRcValuesFrame(rcValues);
    rcValues = getSpektrumRcValuesForRadio();
    radioSendRcValuesFrame(rcValues);

    BatteryValues battValues = getBatteryValues();
    serialSendBattValuesFrame(battValues);

    Frame serialFrame = serialReceiveFrame();
    radioSendFrame(serialFrame);
    Frame radioFrame = radioReceiveFrame();
    serialSendFrame(radioFrame);

    handleReceivedFrame(serialFrame);
    //handleReceivedFrame(radioFrame);  //Right now not necessary, but may be if we expand functionalities
  
}

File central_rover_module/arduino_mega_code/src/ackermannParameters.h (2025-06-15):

#ifndef ACKERMANN_STEERING_PARAMETERS_H
#define ACKERMANN_STEERING_PARAMETERS_H

const int d1_distance_front_middle_wheels = 300; //Distance between the front and middle wheel, in mm
const int d2_distance_back_middle_wheels = 275; //Distance between the back and middle wheel, in mm

//Distances between the longitudinal center of the wheel and the longitudinal center of the rover. 
const int d3_front_back_rover_width = 270; //The front and back wheels have the same distance to the longitudinal center of the rover
const int d4_center_rover_width = 300;

const int max_turning_radius = 4000;  //In mm
const int min_turning_radius = 700; //TODO: Change to 600 when I have done more tests with the rover

//TODO: Create extern for shared variables

#endif

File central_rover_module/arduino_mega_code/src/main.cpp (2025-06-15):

/*Mars rover replica - by Pol V*/

//IMPORTANT: We use software PWM which uses TIMER1, we cannot use analogWrite() on pins 13,12,11, as it uses TIMER1 too.
//We must use software PWM because there are not enough usable PWM ports in the arduino mega. 

#include <Arduino.h>

#include "wheelServoManager.h"
#include "motorManager.h"
#include "rcValuesManager.h"
#include "opModeManager.h"
#include "serialCommunication.h"
#include "batteryManager.h"
#include "radioCommunication.h"
#include "receivedFramesHandling.h"
#include "statusDataManager.h"
#include "armServoManager.h"
#include "sensorsManager.h"
#include "headMovementsManager.h"
#include "relayManager.h"
#include "buzzerManager.h"


void setup() {

  //DO NOT ALTER THE POSITION OF THESE 2 LINES//
  setupRelays();
  setServosRelayStatus(false);  //We immediately put the relay that powers the servos in an OPEN position to make sure that no power gets to the servos before the program initializes
  //////////////////////////////////////////////

  setRaspberryPiRelayStatus(false);  //We power off the Raspberry Pi

  setupWheelServos();
  
  setupMotors();

  setupSerial();

  setupRadio();

  setupBuzzer();

  setupBatteryMonitor();

  setupSensors();

  setupHeadServoStepper();

  //DO NOT ALTER THE POSITION OF THESE 2 LINES//
  setServosRelayStatus(true);  //We power up the servos and we send them their initial positions
  setWheelServosStraight();
  //////////////////////////////////////////////

}

void loop() {

  Frame receivedRadioFrame = radioReceiveFrame();
  Frame receivedSerialFrame = serialReceiveFrame();
  handleReceivedFrame(receivedRadioFrame);
  handleReceivedFrame(receivedSerialFrame);
  operationModeExecution();
  Frame statusDataFrame = getStatusDataFrame();
  radioSendFrame(statusDataFrame);
  serialSendFrame(statusDataFrame);

}

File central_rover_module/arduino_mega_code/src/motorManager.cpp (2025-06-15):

#include <Arduino.h>
#include <PalatisSoftPWM.h>

#include "motorManager.h"
#include "wheelServoManager.h"
#include "ackermannParameters.h"


#define FWD true
#define BCK false

#define MOTOR_1 1
#define MOTOR_2 2
#define MOTOR_3 3
#define MOTOR_4 4
#define MOTOR_5 5
#define MOTOR_6 6

#define MOT1_FWD 0  //TODO: Change names to MOT1_FWD_CH (channel)
#define MOT1_BCK 1
#define MOT2_FWD 2
#define MOT2_BCK 3
#define MOT3_FWD 4
#define MOT3_BCK 5

#define MOT4_FWD 6
#define MOT4_BCK 7
#define MOT5_FWD 8
#define MOT5_BCK 9
#define MOT6_FWD 10
#define MOT6_BCK 11


//The rover has two arms, each one with 3 motors and 2 servomotors for steering.

//Right arm motors, from front to back
const int mot1_fwd = 8; //Motor 1 forward rotation pin
const int mot1_bck = 7; //Motor 1 backward rotation pin

const int mot2_fwd = 10;
const int mot2_bck = 9; 

const int mot3_fwd = 12;
const int mot3_bck = 11; 

//Left arm motors, from front to back
const int mot4_fwd = A0; 
const int mot4_bck = A1; 

const int mot5_fwd = A2;
const int mot5_bck = A3; 

const int mot6_fwd = A4;
const int mot6_bck = A5; 

SOFTPWM_DEFINE_PIN8_CHANNEL(MOT1_FWD);
SOFTPWM_DEFINE_PIN7_CHANNEL(MOT1_BCK);
SOFTPWM_DEFINE_PIN10_CHANNEL(MOT2_FWD);
SOFTPWM_DEFINE_PIN9_CHANNEL(MOT2_BCK);
SOFTPWM_DEFINE_PIN12_CHANNEL(MOT3_FWD);
SOFTPWM_DEFINE_PIN11_CHANNEL(MOT3_BCK);

SOFTPWM_DEFINE_PINA0_CHANNEL(MOT4_FWD);
SOFTPWM_DEFINE_PINA1_CHANNEL(MOT4_BCK);
SOFTPWM_DEFINE_PINA2_CHANNEL(MOT5_FWD);
SOFTPWM_DEFINE_PINA3_CHANNEL(MOT5_BCK);
SOFTPWM_DEFINE_PINA4_CHANNEL(MOT6_FWD);
SOFTPWM_DEFINE_PINA5_CHANNEL(MOT6_BCK);

SOFTPWM_DEFINE_OBJECT(12); //Number of Software PWM Channels

int outer_wheels_speed;
int inner_front_back_wheels_speed;
int inner_middle_wheel_speed;

SpeedometerValues speedometerValues = {0, 0, 0};


void setupMotors() {
  PalatisSoftPWM.begin(15); ///15Hz PWM

  pinMode(mot1_fwd, OUTPUT);
  pinMode(mot1_bck, OUTPUT);

  pinMode(mot2_fwd, OUTPUT);
  pinMode(mot2_bck, OUTPUT);

  pinMode(mot3_fwd, OUTPUT);
  pinMode(mot3_bck, OUTPUT);

  pinMode(mot4_fwd, OUTPUT);
  pinMode(mot4_bck, OUTPUT);

  pinMode(mot5_fwd, OUTPUT);
  pinMode(mot5_bck, OUTPUT);

  pinMode(mot6_fwd, OUTPUT);
  pinMode(mot6_bck, OUTPUT);
}

void setMotorSpeed(int motor_num, int speed, bool direction) {

  int mot6_correction_factor = -4; //The mot6 is a bit faster than the rest at low speeds, we apply this correction factor to solve this problem

  if (motor_num == MOTOR_6) {
    speed = speed + mot6_correction_factor;
  }

  if (speed < 0) {
    speed = 0;
  }

  switch (motor_num) {

      case MOTOR_1:
        if (direction == FWD) {
           digitalWrite(mot1_bck, LOW);
           //analogWrite(mot1_fwd, speed);
           PalatisSoftPWM.set(MOT1_FWD, speed);
        } else {
          digitalWrite(mot1_fwd, LOW);
          //analogWrite(mot1_bck, speed);
          PalatisSoftPWM.set(MOT1_BCK, speed);
        }
        break;

      case MOTOR_2:
        if (direction == FWD) {
           digitalWrite(mot2_bck, LOW);
           //analogWrite(mot2_fwd, speed);
           PalatisSoftPWM.set(MOT2_FWD, speed);
        } else {
          digitalWrite(mot2_fwd, LOW);
          //analogWrite(mot2_bck, speed);
          PalatisSoftPWM.set(MOT2_BCK, speed);
        }
        break;

      case MOTOR_3:
        if (direction == FWD) {
           digitalWrite(mot3_bck, LOW);
           //analogWrite(mot3_fwd, speed);
           PalatisSoftPWM.set(MOT3_FWD, speed);
        } else {
          digitalWrite(mot3_fwd, LOW);
          //analogWrite(mot3_bck, speed);
          PalatisSoftPWM.set(MOT3_BCK, speed);
        }
        break;

      case MOTOR_4:
        if (direction == FWD) {
           digitalWrite(mot4_bck, LOW);
           //analogWrite(mot4_fwd, speed);
           PalatisSoftPWM.set(MOT4_FWD, speed);
        } else {
          digitalWrite(mot4_fwd, LOW);
          //analogWrite(mot4_bck, speed);
          PalatisSoftPWM.set(MOT4_BCK, speed);
        }
        break;

      case MOTOR_5:
        if (direction == FWD) {
           digitalWrite(mot5_bck, LOW);
           //analogWrite(mot5_fwd, speed);
           PalatisSoftPWM.set(MOT5_FWD, speed);
        } else {
          digitalWrite(mot5_fwd, LOW);
          //analogWrite(mot5_bck, speed);
          PalatisSoftPWM.set(MOT5_BCK, speed);
        }
        break;

      case MOTOR_6:
        if (direction == FWD) {
           digitalWrite(mot6_bck, LOW);
           //analogWrite(mot6_fwd, speed);
            PalatisSoftPWM.set(MOT6_FWD, speed);
        } else {
          digitalWrite(mot6_fwd, LOW);
          //analogWrite(mot6_bck, speed);
          PalatisSoftPWM.set(MOT6_BCK, speed);
        }
        break;

      default:
        break;

  }

}

void stopMotors() {

  setMotorSpeed(MOTOR_1, 0, FWD);
  setMotorSpeed(MOTOR_2, 0, FWD);
  setMotorSpeed(MOTOR_3, 0, FWD);
  setMotorSpeed(MOTOR_4, 0, FWD);
  setMotorSpeed(MOTOR_5, 0, FWD);
  setMotorSpeed(MOTOR_6, 0, FWD);

  setMotorSpeed(MOTOR_1, 0, BCK);
  setMotorSpeed(MOTOR_2, 0, BCK);
  setMotorSpeed(MOTOR_3, 0, BCK);
  setMotorSpeed(MOTOR_4, 0, BCK);
  setMotorSpeed(MOTOR_5, 0, BCK);
  setMotorSpeed(MOTOR_6, 0, BCK);

}
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

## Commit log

2024-07-08 First commit with ESP32S3 screen template
2024-07-09 First commit with existing code from Arduino IDE
2024-08-04 Added custom flash partition scheme to maximize app space
    [max_app_with_16MB_flash.csv]
2024-08-08 Changed board to arduino nano and lowered baud rate
2024-08-13 Implemented Serial protocol using library that enables the transfer of structs via serial. Added software Serial in order to free the only hardware Serial for debug purposes. Used millis() instead of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
2024-08-14 Used NRF24 library to receive data from a custom Rc transmitter that uses NRF24. Changedthe nano board to one that uses the new Bootloader as the previous nano did not work with NRF24 library.
    [main.cpp]
2024-08-14 Increased time between send of serial values to avoid saturation of receiver
    [main.cpp]
2024-08-14 Created small frame struct that is sent via serial
2024-12-29 Created functions to calculate bat percentage and make buzz sounds. Modified comments. Added new TODOs.
    [main.cpp]
2025-01-09 Created folder for UI SQ files. Created button click test function.
2025-01-10 Fixed slow rc values update
    [screenController.cpp]
2025-01-11 Image buttons in home screen finished
2025-01-12 Created exclusion logic for main buttons on home screen
2025-01-12 Finished disabled states of main buttons in home screen
2025-01-12 Expanded exclusion logic for buttons on home screen
2025-01-17 All tab views implemented. Created functions to handle config tab buttons and selector.
2025-01-18 Serial msg from Nano to ESP32 work with new frame struct. Values are displayed in screen
2025-01-18 Serial msg from Nano to ESP32 work with new frame struct
2025-01-18 Code restructuration and frameTypes adition. New bidirectional serial test done.
2025-01-18 Bidirectional serial test with frameTypes done
2025-01-19 Tests with bidirectional serial and radio completed. Rc battery values are now available on the screen.
2025-01-30 Improved radio link status and 360 mode movement sections by replacing delays with millis
2025-02-10 Changed Frame field type to allow negatives. Small restructuring.
2025-02-10 Added Frame logic into main rover. Conventional mode works with Frames; other modes left to do and testing left to do
2025-02-10 Send rcValues frame with radio implemented. Changed Frame field type. Validation of RcValues left to do.
2025-02-10 Added new button in home to control sending of RcValues. Moved original button to config tab.
2025-02-10 360 rotation mode works with Frame system and screen.
2025-02-11 Inverted joysticks. Cleaned code.
    [main.cpp, motorManager.cpp]
2025-02-17 Battery values are now sent to RC. Created data manager module.
2025-02-17 uiObjVisibility fix. Now rover battery values are received and displayed.
    [receivedFramesHandling.cpp, uiObjVisibilityManager.cpp]
2025-02-17 Improved functions related to battery values
2025-02-18 Robotic arm with initial positions working
2025-02-18 Small change in folded arm positions
2025-02-19 Robotic arm control with RC fully works. Only testing and minor ajustments left to do.
2025-02-19 Added function for ArmServoSelection button
2025-02-21 Now, the robotic arm servos do not hold position until the robotic arm control mode is clicked for the first time. Servo4 initializes in a different position so that it is easier to go away from the 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
2025-02-21 AUX values are now corrected
    [main.cpp]
2025-02-21 AUX1 now is used for robotic arm control and toggles a switch in the screen.
2025-02-24 Pressure sensor tests working. BME280 libraries added
2025-02-25 Increased time between readings and sendings of RcValues for Radio and Serial, in order to increase the performance for receiving frames (previously we had some issues with the environmentalValues re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
    [main.cpp]
2025-03-02 Initial home position finding for stepper done. Testing left to do.
2025-03-08 New relay for RPI added. Initial serial communication tests with RPI work.
2025-03-09 Bidirectional serial communication test with RPI and frames working.
2025-03-09 Bidirectional serial communication test with Arduino and frames working.
2025-03-09 Communication tests with send and receive frames functions
2025-03-09 Status frames are now sent to RPI and received from RPI. RPI relay now works with screen SW.
2025-03-09 Status frames from RPI are now received and displayed on the screen. RPI power relay now works with screen SW.
2025-03-09 Status frames from RPI are now sent. Threads are used to send and receive frames. Created new functions to organize code. Modulation left to do.
2025-03-15 Values from frame conversion implemented
2025-03-15 Small fixes on textField size and component name
    [receivedFramesHandling.cpp]
2025-03-16 Created button to start and stop the video feed thread
2025-03-26 Camera feed status is now sent to rover and RC
2025-03-27 Added low battery buzz. Cleaned and improved code.
    [main.cpp]
2025-06-15 Transferred remote_control_touchscreen code from the old repositories
    [max_app_with_16MB_flash.csv]
2025-06-17 Added 3D design file. Added designs explanation and images.
    [RC_touchscreen_cases_Spektrum_DX8.f3d]
2025-06-17 Added schematics and hardware explanation for every module.
2025-06-17 Added assembly section and explanation.
2025-06-18 Corrected errors in assembly README. Improved remote_control_touchscreen module README.
2025-06-18 Added rover and RC assembly images
2025-06-18 Improved main README with assembly folder references.
2025-10-12 Added new frame types definitions
2025-10-12 Renamed some folders and improved main README
    [max_app_with_16MB_flash.csv]
2025-10-12 Deleted copies of code of all the project modules
    [max_app_with_16MB_flash.csv]
2025-10-20 Improved READMEs and added project report PDF
    [main_materials_and_parts_list.xlsx]
2025-11-19 README improvements. Added more detailed hardware components list.
    [main_materials_and_parts_list.xlsx]
2025-12-30 Added new GIF for demo video. Added a new mechanical parts list. Added rover 3D design of some parts and improved README.
    [rover_modified_and_new_parts.f3d]
